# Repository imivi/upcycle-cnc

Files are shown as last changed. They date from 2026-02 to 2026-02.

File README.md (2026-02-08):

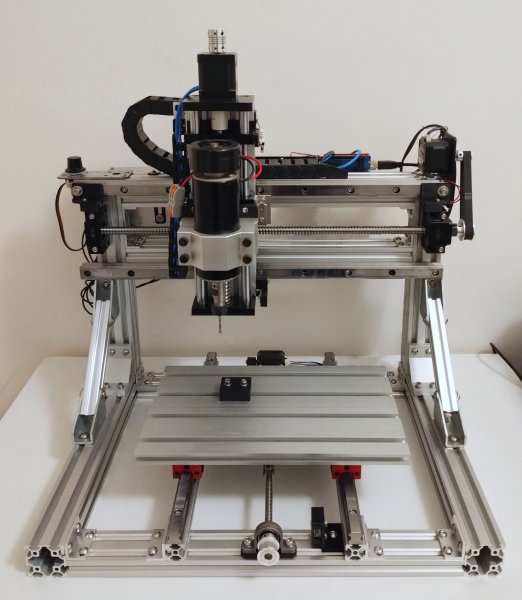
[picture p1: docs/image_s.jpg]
UpCycle CNC


# UpCycle CNC

UpCycle CNC is an open source DIY CNC design that reuses parts from the popular 3018 CNC.

It features a 30x18 cm cutting area with around 9 cm of Z travel.

The full part list (bill of materials) is included in `cnc_bom.csv`.

Requires the 3D printed parts found in the `printed-parts` directory. Freecad, STEP and STL files are included.

The endstop brackets are available here:

* [Sculpfun S10 Limit Switch Mount](https://www.printables.com/model/898865-sculpfun-s10-limit-switch-mount/files)

## How to install GRBL onto an Arduino Uno

1. Download the GRBL firmware (as zip file): https://github.com/gnea/grbl
2. Unzip and then zip the **grbl** subdirectory
3. In the Arduino IDE, Sketch > include library... > add .zip library
4. Select the zipped grbl subdirectory
5. File > examples > grblUpload
6. Upload the sketch

## Wiring the relay module to toggle the spindle

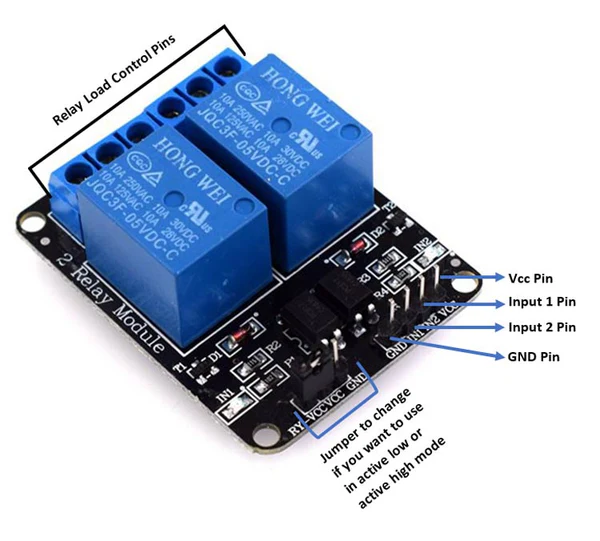
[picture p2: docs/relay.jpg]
Relay module


In order to use the relay to toggle the spindle, we must customize the GRBL configuration.

We have to modify the grbl configuration file (config.h) and reupload GRBL:

* **Windows:**`C:\Users\[YourName]\Documents\Arduino\libraries\grbl\config.h`

* **Linux:**`~/Arduino/libraries/grbl/config.h`

1. open `config.h`
2. comment "#define VARIABLE_SPINDLE" to disable spindle PWM control (only on/off)
3. uncomment "INVERT_SPINDLE_ENABLE_PIN" so that the enable pin is HIGH by default, which turns OFF the relay (which has an inverted behavior)
4. reupload GRBL

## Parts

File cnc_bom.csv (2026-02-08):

category | part | pcs | note
motion | Hgr20 rail 400-500mm | 2 | for X axis
 | Hgr15 rail 350mm | 2 | for Y axis
 | Hgh20 carriage | 2 | for X axis
 | Hgh15 carriage | 4 | for Y axis
 | Lead screw 350 mm | 1 | for Y axis
 | Lead screw nut | 1 | for Y axis, can reuse from 3018
 | Nema 17 stepper motors | 3 | can reuse from 3018
 | Lead screw |  | for Y axis
 | Coupling from 5mm to 8mm | 1 | for Y axis motor
 | Gt2 pulley, 40t, 10mm width | 1 | for X axis
 | Gt2 belt, 260mm length, 10mm width | 1 | for X axis
 | Sfu1204 ball screw | 1 | for X axis
 | Sfu1204 nut + housing | 1 | for X axis
 | Bk10 bearing block | 1 | for X axis
 | Bf10 bearing block | 1 | for X axis
 | KP08 bearing block | 1 | for Y axis
frame | 4040 aluminum profile, 350mm | 2
 | 4040 aluminum profile, 400mm | 2
 | 4040 aluminum profile, 300mm | 2
 | 15180 aluminum bed | 1 | can reuse from 3018
 | Gas spring “u” brackets | 2 | for upright reinforcement
 | 2020 aluminum profile, 200mm | 2 | for upright reinforcement
 | 2020 aluminum profile, 350mm | 2 | as Y axis spacers
 | 2020 aluminum profile, 400mm | 2 | for the base
 | Aluminum angle brackets for 4040 profiles | 2
 | Premade z axis assembly | 1 | SFU1605, 150mm travel
 | Aluminum l bracket | 12
 | M5 screws, length 8 mm | 56 | for L brackets
 | M5 screws, length 30 mm | 4 | for ball screw bearing blocks
 | M5 screws, length 14 mm | 10 | for HGR20 rails
 | M4 screws, length 14 mm | 10 | for HGR15 rails
 | M3 screws, 10 mm length | 12 | for stepper motors
 | Nema 17 bracket | 1 | for Y axis
 | Nema 23 bracket | 1 | for X axis
electronics & wiring | Drag chain 40x15mm | 1
 | Spindle cable (2 wires) | 1
 | Limit switches | 6 | 3 are enough if using soft limits
 | Arduino Uno | 1
 | CNC shield | 1
 | Relay module | 1 | to control the spindle
 | Motor power supply (12-24V) | 1 | for example Meanwell LRS-200-24
other | Spindle (500w) | 1
 | Spindle psu, 100v | 1
 | Spindle mount | 1

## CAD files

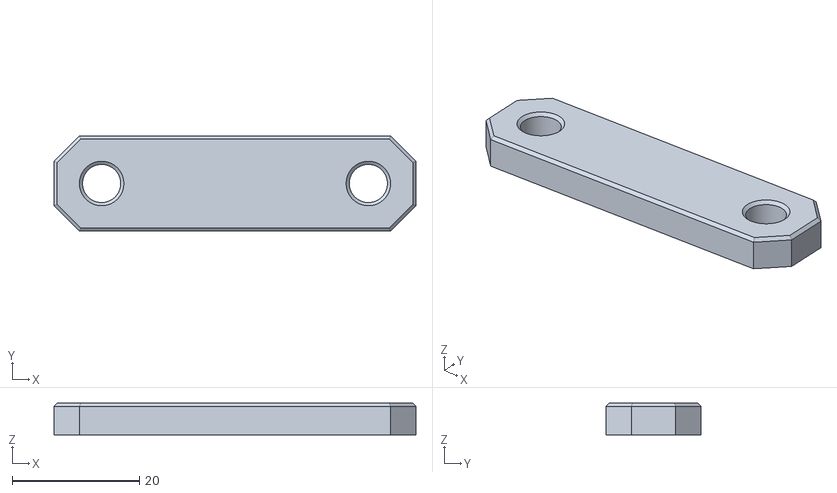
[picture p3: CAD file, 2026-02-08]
printed-parts/Spacer for KP08-Body.stl
57.0 x 15.0 x 5.00

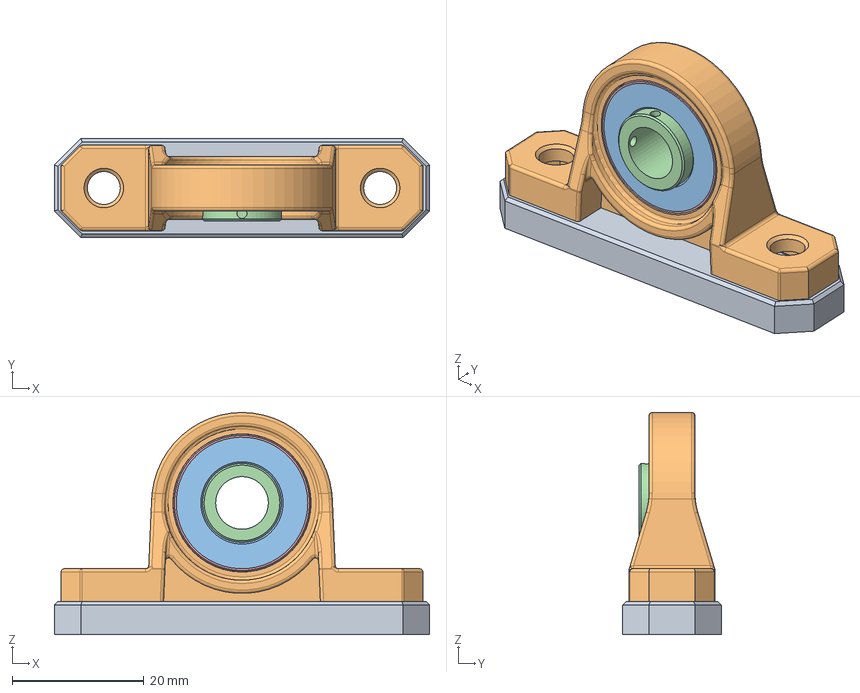
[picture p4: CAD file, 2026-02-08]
printed-parts/Spacer for KP08.FCStd
57.0 x 15.0 x 33.8 mm
KP08 SUPPORT BEARING-Edited v2
KP08 SUPPORT BEARING-Edited v003
KP08 SUPPORT BEARING-Edited v004
KP08 SUPPORT BEARING-Edited v005

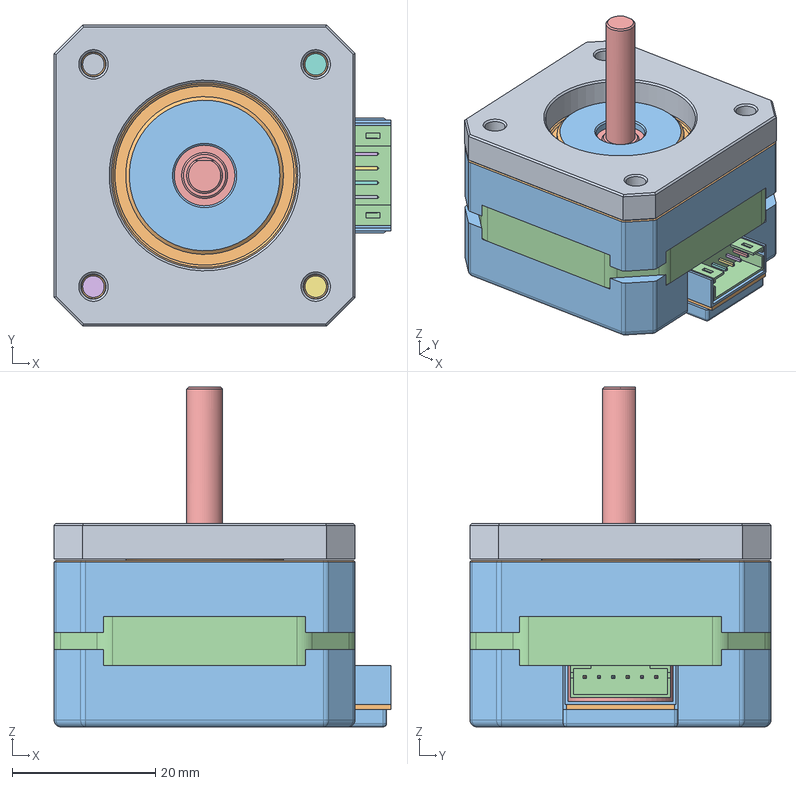
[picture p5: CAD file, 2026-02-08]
printed-parts/Spacer for Z axis motor.FCStd
47.0 x 42.0 x 47.4 mm
M3x12-Screw
M3x12-Screw004
M3x12-Screw005
M3x12-Screw006

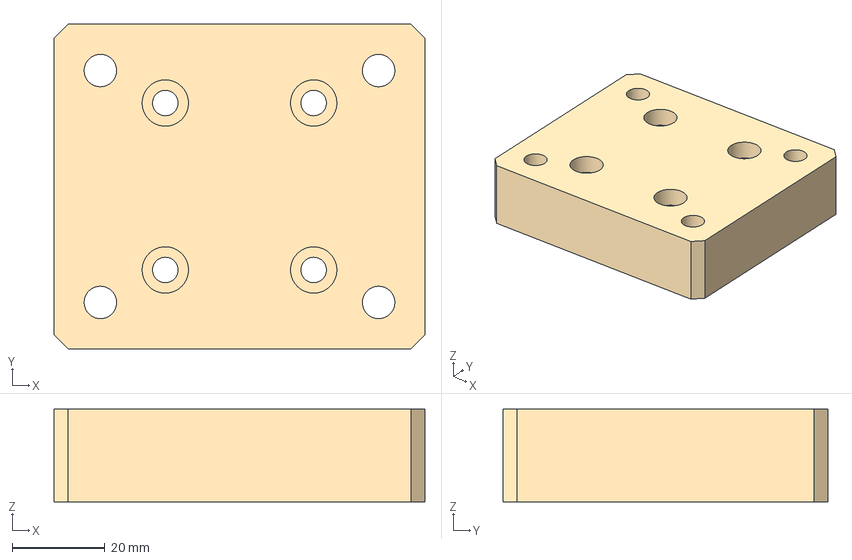
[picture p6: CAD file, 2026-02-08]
printed-parts/HGH20 spacers.step
80.0 x 70.0 x 20.0 mm

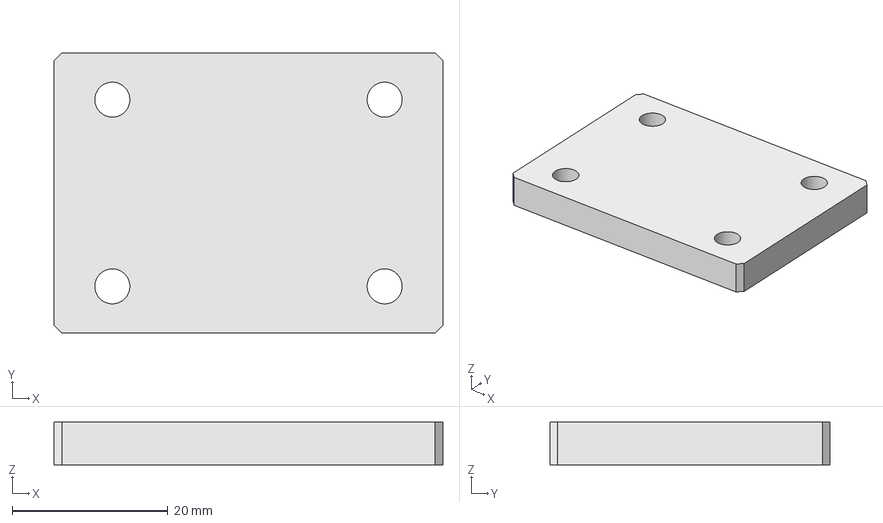
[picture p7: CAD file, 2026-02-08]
printed-parts/SFU1204 spacer.step
50.0 x 36.0 x 5.50 mm

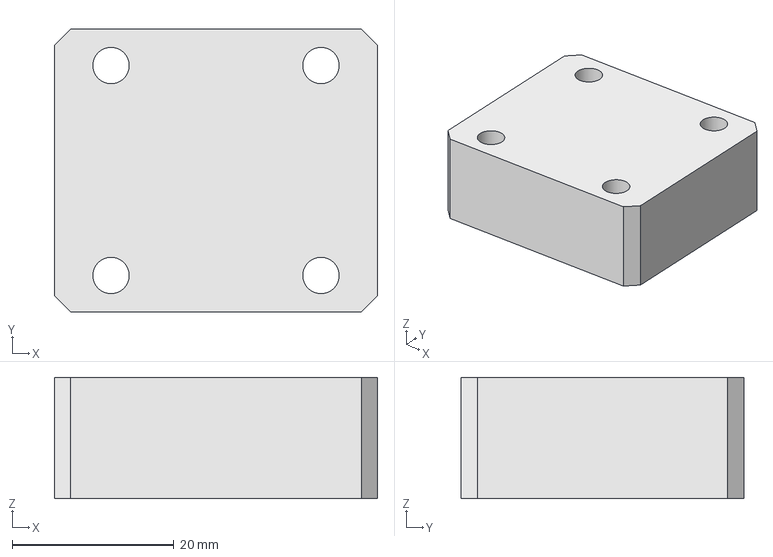
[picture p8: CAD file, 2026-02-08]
printed-parts/HGH15 spacer.step
40.0 x 35.0 x 15.0 mm

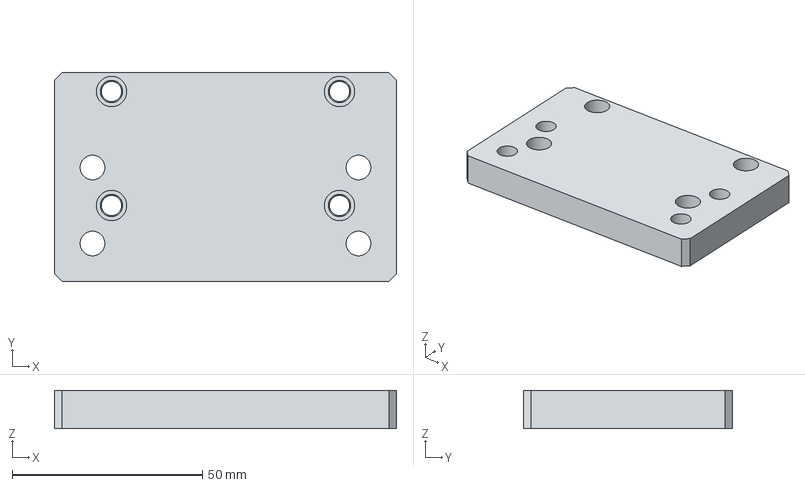
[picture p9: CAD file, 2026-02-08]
printed-parts/Spindle bracket.step
90.0 x 55.0 x 10.0 mm

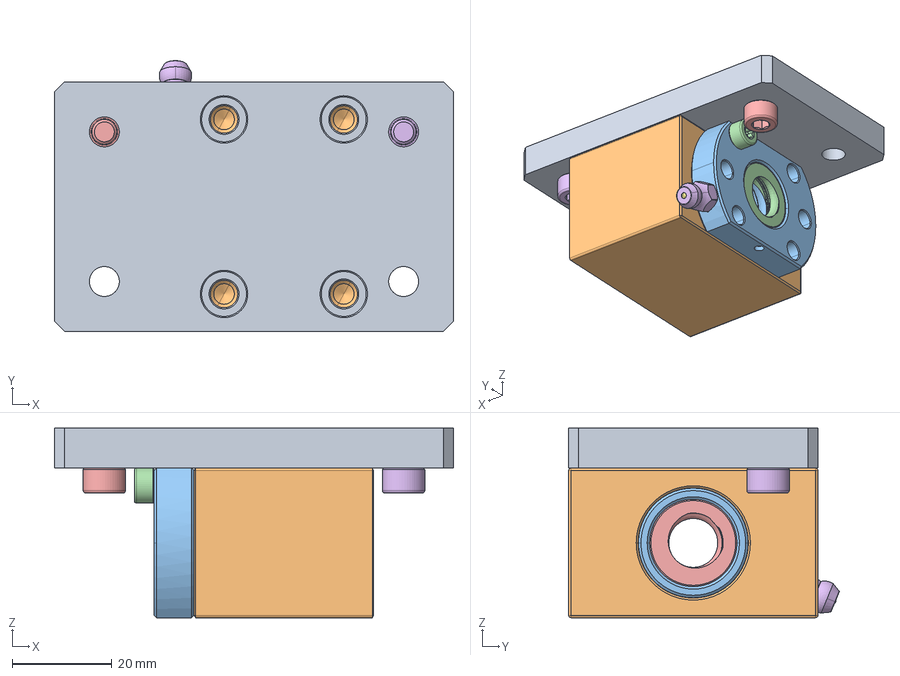
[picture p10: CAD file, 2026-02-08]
printed-parts/Bracket for X axis ball screw.FCStd
80.0 x 54.3 x 38.0 mm
SFU1204 housing
SFU Ball Nut_1204-3
SFU1204 Washer Front
SFU1204 Washer Back
Grease Nipple A_A M6x1.00
Steel Ball_O 2.50
socket set screw cone point_iso_ISO 4027 - M3 x 5-C
socket set screw cone point_iso_ISO 4027 - M3 x 5-C001
socket set screw cone point_iso_ISO 4027 - M3 x 2.5-C
socket set screw cone point_iso_ISO 4027 - M3 x 2.5-C001
M4x10-Screw
M5x8-Screw
M5x8-Screw001

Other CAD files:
printed-parts/Bracket for X axis ball screw.stl
printed-parts/HGH15 spacer.FCStd
printed-parts/HGH15 spacer.stl
printed-parts/HGH20 spacers.FCStd
printed-parts/HGH20 spacers.stl
printed-parts/SFU1204 spacer.FCStd
printed-parts/SFU1204 spacer.stl
printed-parts/Spacer for Z axis motor.stl
printed-parts/Spindle bracket.FCStd
printed-parts/Spindle bracket.stl

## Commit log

2026-02-08 Add bom and 3d printed files
    [HGH15 spacer.FCStd, HGH15 spacer.step, HGH15 spacer.stl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]
2026-02-08 Update bom
    [cnc_bom.csv]
